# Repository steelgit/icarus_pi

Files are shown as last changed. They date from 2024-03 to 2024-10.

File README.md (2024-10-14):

# Icarus 🪽

Icarus is an open-source project that students or hobbyists can use as a base to gain experience with ROS2, SLAM, and Nav2. It is also a way for us to share our love of robotics! 

Icarus is a four-wheeled, mecanum-drive robot capable of manual and autonomous navigation. This is the project's main repository and contains all of the information and code to create the physical robot. Our sub-repo ([Icarus Jetson Nano Repository](https://github.com/steelgit/icarus_nano)) contains all of the information required to add autonomous navigation to the robot and can be used without recreating Icarus.

<br />

Icarus Video Video of Icarus Operating Autonomously

<br />
<br />

# Initial Run

>[Install the pigpio library](https://abyz.me.uk/rpi/pigpio/download.html)

>To install all of the required dependencies from the package.xml run:

    rosdep update --include-eol-distros    
<br />

    rosdep install --from-paths src -y --ignore-src --rosdistro foxy

<br />
<br />

# To Launch Icarus

>On startup, launch the PiGPIO Daemon using:

    sudo pigpiod

>Launch the robot!

    ros2 launch icarus_pi launch_robot.launch.py 

<br />
<br />

# To Launch Icarus in Simulation

>With Planar Controller:

    ros2 launch icarus_pi launch_sim_planar.launch.py 

>With Mecanum Controller:

    ros2 launch icarus_pi launch_sim_mecanum.launch.py 

<br />
<br />

# Materials List

Some of our core components include:

- Jetson Nano
- Raspberry Pi 4
- Motors with Quadrature Encoders
- Motor Controllers (L298N)
- 2-D LiDAR
- Raspberry Pi Camera V2
- Mecanum Wheels

<br />

A full list of our materials can be found on our [Materials List ](/docs/Materials%20List.pdf).

<br />
<br />

# Software

The Software for the Icarus Project is split between two devices, which requires having two different Ros2 workspaces.  The Raspberry Pi uses the Icarus_pi workspace in this repo, which contains the three main custom ROS2 packages: icarus_interface, icarus_pi, and mech_drive_controller.  Icarus_pi is the starting point for Icarus architecture and contains the robot description, launch files, and robot configuration files.  Except for PID tuning, all unique robot intrinsics are stored here and can be modified to fit different setups.  Icarus_interface is the Ros2 interface to the motor and encoders.  It leverages the PiGPIOd library to control GPIO signals on the Raspberry Pi, and will perform PID control when the interface is written to.  Finally, the mech_drive_controller is a custom ROS2 controller which allows two linear and one rotational movements.  These three packages work in tandem to manage all movement of the Icarus Robot and can run independent of icarus_nano. Icarus_nano contains three main ROS2 packages: autonomy, rplidar_ros, and camera_publisher. The autonomy package extends the slam_toolbox and Nav2 packages to enable support for holonmonic drive roborts. The rplidar_ros is cloned from the official Slamtec repository, (linked in the References section), and takes data from the physical LiDAR and translates it into a laser scan topic. The camera_publisher topic takes in information from our camera stream and publishes it so that we can see what the robot sees through RVIZ. 

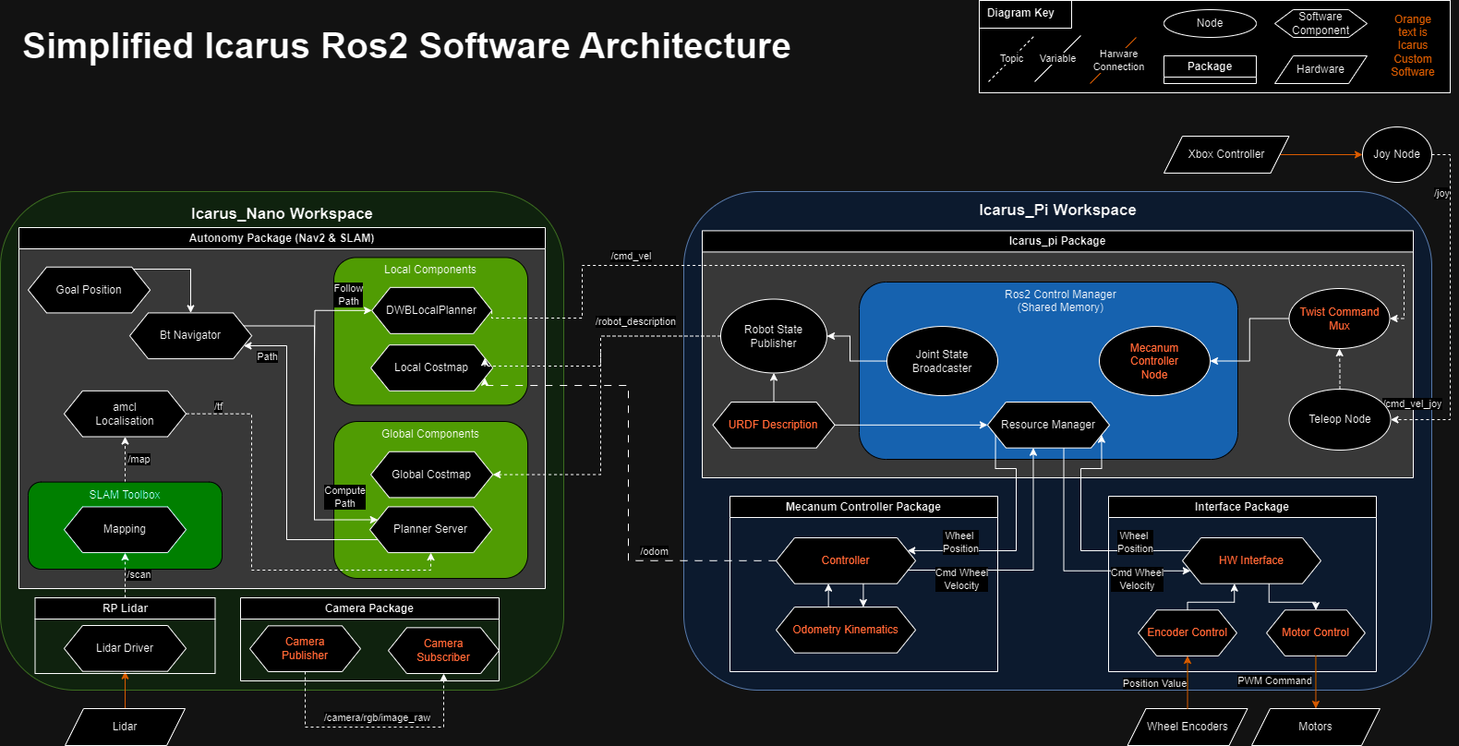
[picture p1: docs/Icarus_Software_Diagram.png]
Icarus Software Diagram Icarus Software Design


<br />
<br />

# Mechanical

The design of this robot was inspired by the turtlebot-burger educational platform. This design allows for a high degree of flexibility in the placement of components. Additionally, due to the modular design philosophy here, its possible to add, remove, or swap out new parts and sensors as you see fit. If desired, you can create your own custom fixtures and components to mount onto your robot as you see fit.
The mounting holes on the base plates have an initial diameter of 4.5mm in order for m3 flathead screws to sit flush within the plate, and then we have a 3.5mm diameter hole that's also designed for m3 screws; with a center-to-center distance of 20mm between each hole.
for a more vibration-resistant fit, add in threaded brass inserts to your mounting components by melting them in via soldering iron.

<br />

#### Mechanical Assembly

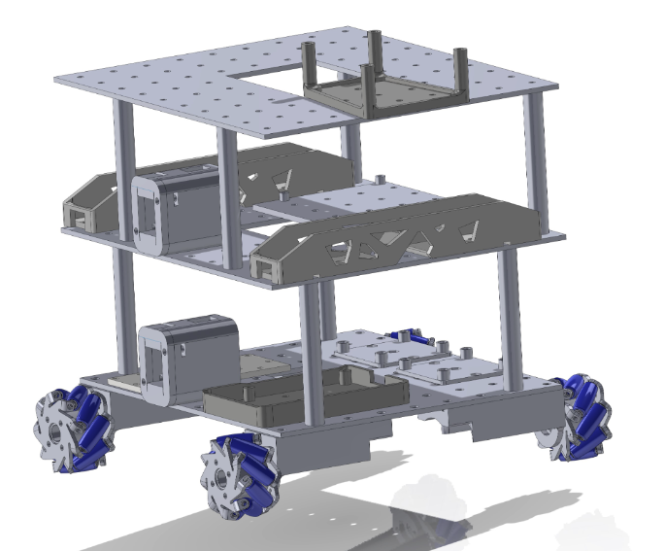
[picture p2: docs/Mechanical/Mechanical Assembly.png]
Icarus Mechanical Design


<br />

A more in-depth description of our mechanical design, as well as our STL files, can be found in our [Mechanical Documentation](/docs/Mechanical/Mechanical%20README.md).

<br />
<br />

# Electrical

Our electrical design was formulated around the core components that we wanted to use. These core components are listed above in the Material List section. We wanted to be able to operate the robot for a good amount of time before we needed to swap out or charge the batteries so that we could work on the project or test things for hours at a time. Because of this, and the fact that we used 12V motors, we opted for 
two 11.1 V, 5000 milli-amp hour batteries, one to power the motors, and one to power the rest of our electronics. We decided to solder as many of the components as we could for durability. The motors used jumper cable connections and since these could not be soldered easily, we decided to secure the connections with a layer of kapton tape. Our electrical diagram below shows how all of our components interact with each other.

<br />

#### Electrical Diagram

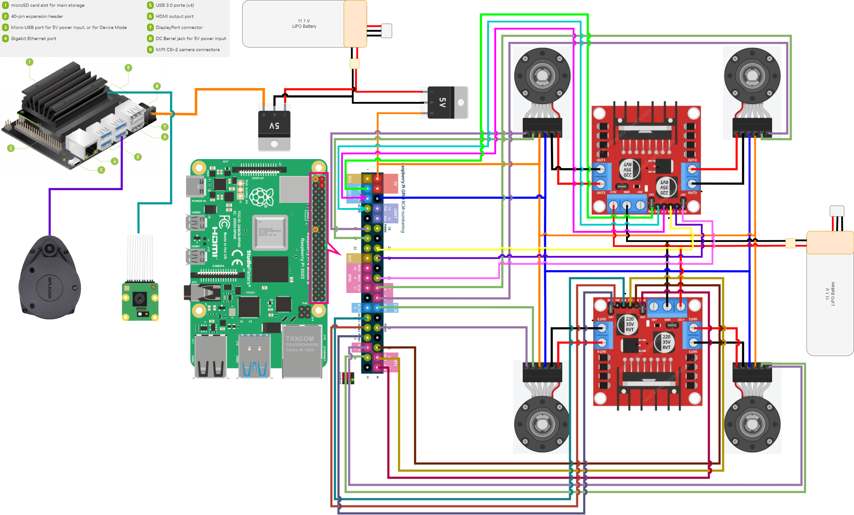
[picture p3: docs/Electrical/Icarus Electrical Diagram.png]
Icarus Electrical Diagram


<br />

A more in-depth description of our electrical design, as well as our [electrical schematic](docs/Electrical/Icarus%20Electrical%20Schematic.pdf) and [pinout descriptions](/docs/Electrical/Motor%20Connections%20Table.pdf), can be found in our [Electrical Documentation](/docs/Electrical/Electrical%20README.md).

<br />
<br />

# Mecanum Wheels

The Icarus Robot was created with the goal of controlling four Mecanum wheels.  Mecanum wheels that contain a circular array of smaller angled wheels.  This wheel arrangement allows movement in both the x and y linear directions, while still allowing a yaw rotation.  This also allows the robot to diagonally strafe or rotate while moving based on precise control of wheel speed and direction.  This required creating a custom controller package based on Ros2 control diff drive to allow the additional degree of movement.

<br />

#### Mecanum Wheel Kinematic Model

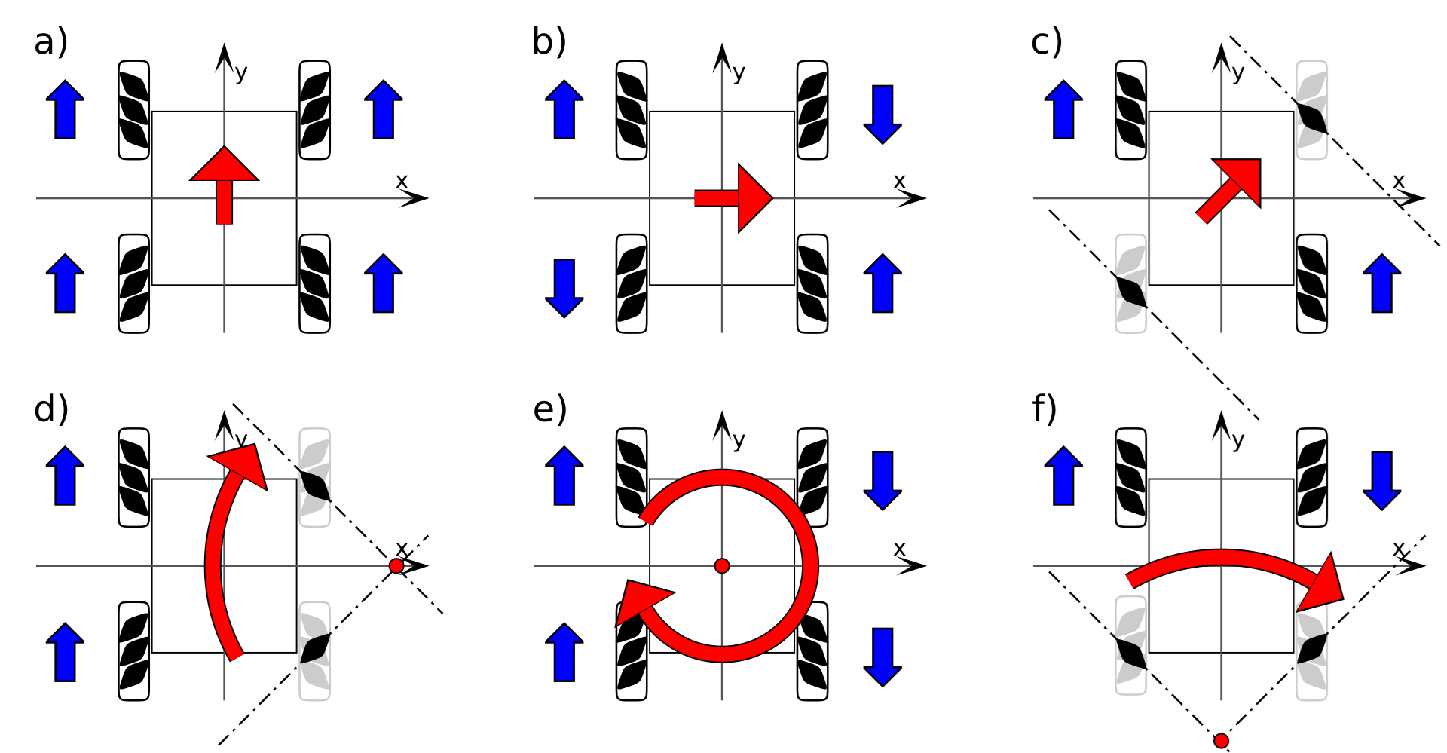
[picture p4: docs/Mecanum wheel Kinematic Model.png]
Mecanum Wheel Kinematic Model


#### Mecanum Wheel CAD Model

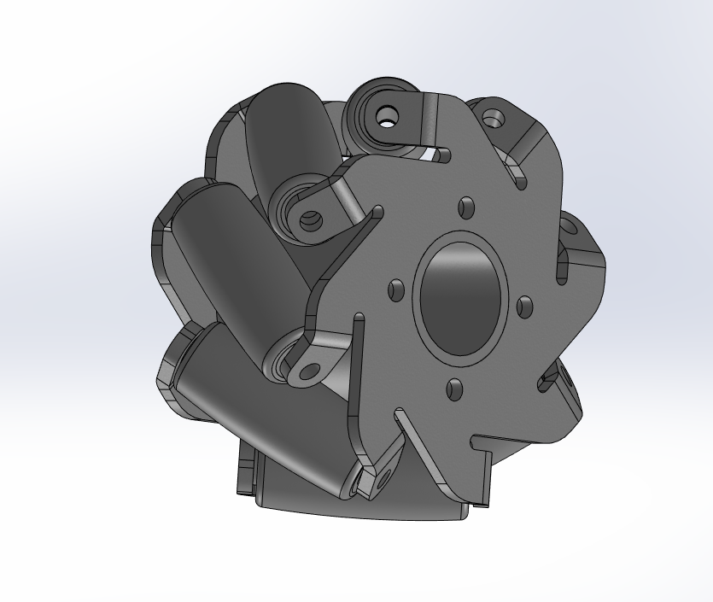
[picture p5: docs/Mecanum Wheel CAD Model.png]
Mecanum Wheel CAD Model


<br />

A more in-depth description of the various software challenges we faced with mecanum wheels can be found in our [Mecanum Wheel Documentation](/docs/Mecanum%20Wheel%20README.md).

<br />
<br />

# Lessons Learned & Future Improvements

Overall, we are quite happy with how Icarus turned out! However, looking back on our implementation, there are some things we would have done differently to achieve similar results while making our lives a little easier in the process. Some items that would have provided some relief to our major pain points include a more modular mechanical design, specifically for our component mounts, a simplified electrical design, and a change in the microcontrollers used. Addressing these issues would have allowed us to better utilize our time spent on Icarus. Below, we have detailed more improvements we would make in our 3 major categories: software, electrical, and mechanical. 

<br />

### Software

Our software design went through many iterations and required countless hours of discussion and design to get to our final product.  We learned three main lessons throughout the project's timeline when it came to our software process.  First, we should have filled out and shored up the project's foundational code before adding more software layers.  Debugging Nav2 and controller issues took significantly longer due to errors in our robot description and odometry calculation.  These could have been caught earlier and saved time later in the project if they had been a step at a time instead of simultaneously with the higher level software.  More early development in simulation would have been one way to catch these early issues.  The next lesson learned was that the group could have been more careful when researching embedded software version limits before progressing too far into setup.  The Jetson Nano cannot run Foxy or Humble natively, and Xubuntu on the Jetson Nano could only run up to Foxy.  This caused a version mismatch between some of our devices and the embedded system that led to errors later in the development cycle.  Finally, establish a common workflow for group members.  Our personal devices were setup independently, which caused members to not have the same tools or organization.  More communication on this area of the project would have made certain areas of our workflow run smoother.

-Be extra careful when reading hardware documentation.  Our LiDAR was mounted backwards, and caused the robot to move in unexpected directions.

<br />

### Electrical

The thing that we would like to improve upon in the future would be to simplify our electrical design. Our design greatly exceeds what was needed for the project, in terms of things like processing power and battery life. This is beneficial because we could easily integrate more features or sensors into the base design without worrying too much about power considerations or having to swap out the batteries too often. However, this also made the design take longer to assemble, which was detrimental to our objectives since we wanted to focus more on the software side of this project.

The switches were a nice addition, however, they could be removed to simplify the power and ground connections. Since the battery connectors are easily accessible, the system can be quickly de-energized without switches by simply disconnecting the connectors. There were also a couple of instances where wires had to be spliced 3 or more times. Creating these splices took us a little longer than initially expected, so using terminal blocks for connections instead of solder could make the assembly process quicker. Smaller milli-amp hour batteries could also be used to save on cost.

The biggest electrical change we would make would be to switch out our microcontrollers. Having the processing power of the Raspberry Pi and the Jetson Nano was nice, however, we could have accomplished everything we did with an Arduino and either a Raspberry Pi or Jetson Nano. The Arduino would control our motors and the rest of the processing would be offloaded onto the other microcontroller.

<br />

### Mechanical

It was never a wise decision to design something with the idea that we would never move the component from its position, or that it would need to be removed from its mounting area. Always design with ease of assembly and disassembly in mind

Make use of not only the horizontal space available on a given surface. If it's more convenient for assembly, create designs that take advantage of the vertical space given,
i.e.: mounting this vertically, upside down, stacked, etc.
<br />
<br />

# References

- [ROS2 Foxy Official Documentation](https://docs.ros.org/en/foxy/index.html)
- [The PiGPIO Library](https://abyz.me.uk/rpi/pigpio/index.html)
- [Articulated Robotics - Build a Mobile Robot with ROS](https://articulatedrobotics.xyz/tutorials/mobile-robot/project-overview)
- [ECAM Eurobot - Mecanum Wheels](https://ecam-eurobot.github.io/Tutorials/mechanical/mecanum.html)
- [Turtlebot3](https://www.turtlebot.com/turtlebot3/)

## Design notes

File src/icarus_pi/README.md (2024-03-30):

## Robot Package Template

This is a GitHub template. You can make your own copy by clicking the green "Use this template" button.

It is recommended that you keep the repo/package name the same, but if you do change it, ensure you do a "Find all" using your IDE (or the built-in GitHub IDE by hitting the `.` key) and rename all instances of `icarus_pi` to whatever your project's name is.

Note that each directory currently has at least one file in it to ensure that git tracks the files (and, consequently, that a fresh clone has direcctories present for CMake to find). These example files can be removed if required (and the directories can be removed if `CMakeLists.txt` is adjusted accordingly).

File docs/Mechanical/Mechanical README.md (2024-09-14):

# Information on Constructing the Robot
The following parts will need to have brass inserts melted into them. We accomplished this by using a soldering iron to heat up the plastic around the mounting holes and then using pliers to slide in the brass inserts.

- Raspberry Pi Holder (only where the pi mounts to the board)
- Motor Holders
- L298N Holder (where L298N mounts to board)
- Supports for each level
- Switch Carriages
- Nano mount
- RPLiDAR mount (where LiDAR mounts to the board, may need a smaller brass insert)

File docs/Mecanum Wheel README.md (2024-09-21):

### Mecanum Information
To provide this range of movement, Icarus is required to calculate individual wheel rotation velocities based on chassis velocity command.  The wheel velocities are calculated using the Mecanum Inverse kinematic formula as shown below.

$$\left(\begin{matrix}
\omega_{fl} &= \frac{1}{r} \left[v_x - v_y - (l_x + l_y)\omega_z \right ] \\ 
\omega_{fr} &= \frac{1}{r} \left[v_x + v_y + (l_x + l_y)\omega_z \right ] \\ 
\omega_{rl} &= \frac{1}{r} \left[v_x + v_y - (l_x + l_y)\omega_z \right ] \\ 
\omega_{rr} &= \frac{1}{r} \left[v_x - v_y + (l_x + l_y)\omega_z \right ] 
\end{matrix}\right)$$

The robot also publishes the Odometry of its movement, so it must calculate its actual speed and position.  Using the motor encoders to find wheel velocity, we use the Mecanum Kinematic Formula shown below to find its chassis velocity.

$$\left(\begin{matrix}
v_x & = (\omega_{fl} + \omega_{fr} + \omega_{rl} + \omega_{rr}) \cdot \frac{r}{4}\\ 
v_y & = (-\omega_{fl} + \omega_{fr} + \omega_{rl} - \omega_{rr}) \cdot \frac{r}{4}\\ 
\omega_z & = (-\omega_{fl} + \omega_{fr} - \omega_{rl} + \omega_{rr}) \cdot \frac{r}{4(l_x + l_y)}
\end{matrix}\right)$$

These equations and diagrams were sourced from the Ecam Eurobot, which can be found under references on the repo main page.

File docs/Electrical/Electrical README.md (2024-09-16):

# Electrical Information

Our electrical schematic below shows how our Raspberry Pi 4 connects to our quadrature motors and motor controller boards. It also highlights what connections are connected directly to our 12V batteries and what connections are connected to our regulated 5V rails. All of our 5V connections are spliced together with a common ground. Our 12V connections do the same.

We soldered together all of our connections, except for the wiring for our motors. These connections needed jumper cables so we used a pin-to-pin jumper connected to a pin-to-socket jumper to give us the length we needed. We wrapped the connection between the pin and socket with Kapton tape for added security and isolation. We also added a Raspberry Pi hat to the Raspberry Pi 4 that allowed us to solder those connections to ensure they would not vibrate loose. 

We added 5V regulators to our circuit to provide surge protection for our microcontrollers. This was needed since neither the Jetson Nano nor the Raspberry Pi 4 have proper over-voltage protection. Both of these microcontrollers need a microSD card. A 16 GB microSD will suffice for the features we have added, but to allow for new features, we would strongly recommend at least a 32 GB microSD card.

The LiDAR connects to the Jetson Nano via the USB ports. The Raspberry Pi 4 connects to the Jetson Nano via the CSI connector port. Due to the nominal current requirements of these two peripherals and the current needs of the Jetson Nano, it is necessary to power the Jetson Nano with the barrel jack rather than the micro-USB connection.

#### Electrical Schematic
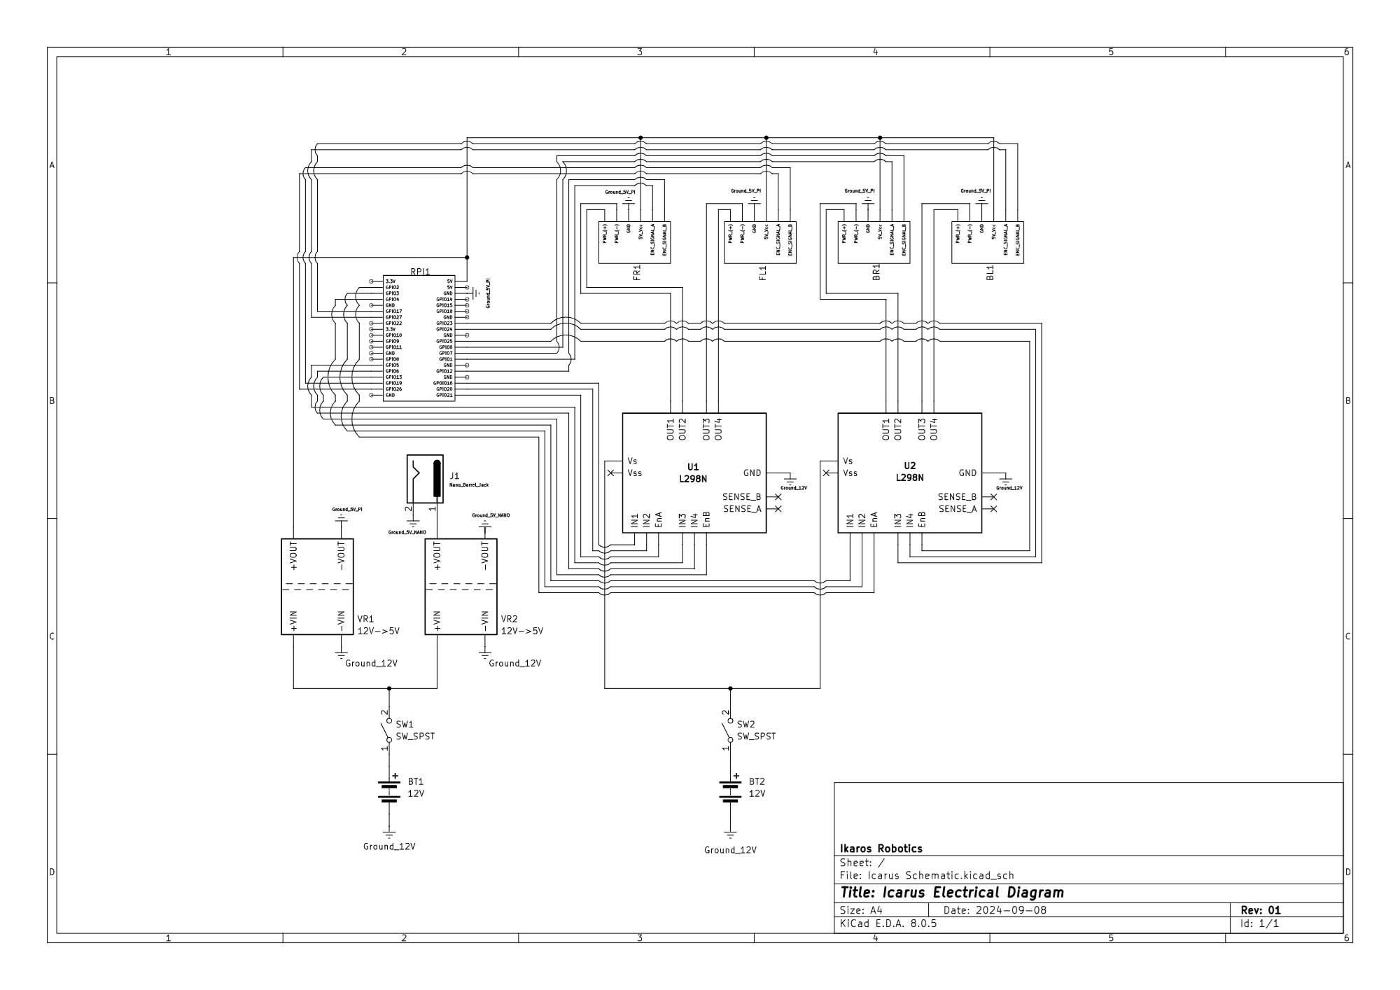
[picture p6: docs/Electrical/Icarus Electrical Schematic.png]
Icarus Electrical Schematic


#### Motor Pinout Table
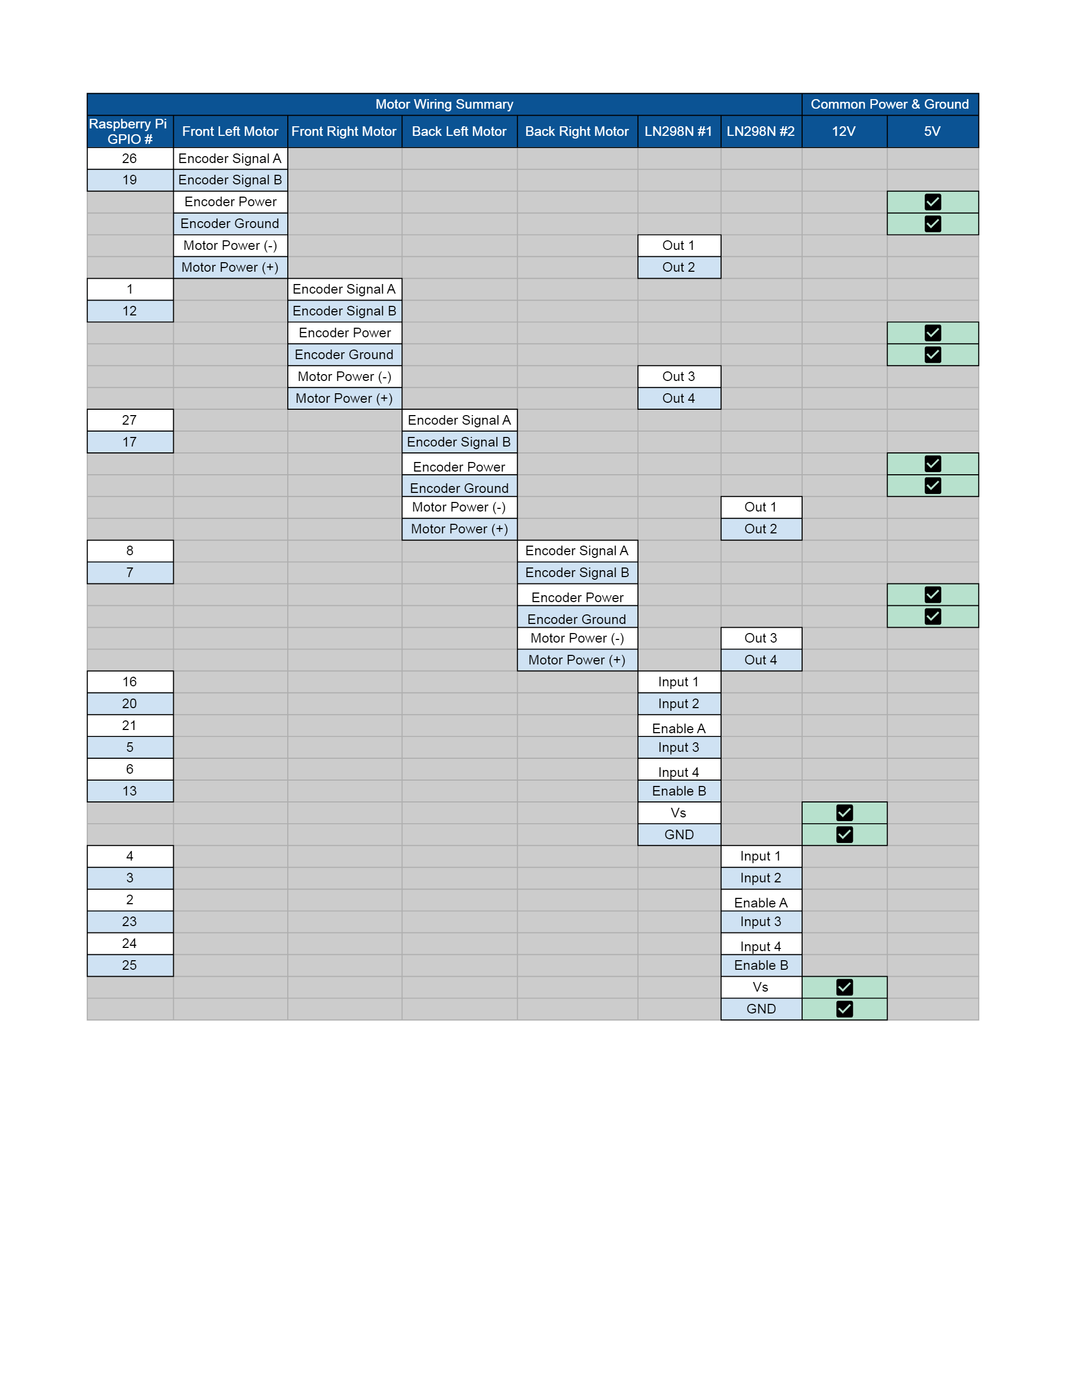
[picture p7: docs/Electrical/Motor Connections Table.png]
Icarus Motor Connections Table


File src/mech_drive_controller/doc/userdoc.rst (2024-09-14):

.. _mech_drive_controller_userdoc:

mech_drive_controller
=====================

Controller for mobile robots with Mecanum drive.
Input for control are robot body velocity commands which are translated to wheel commands for the Mecanum drive base.
Odometry is computed from hardware feedback and published.

Velocity commands
-----------------

The controller works with a velocity twist from which it extracts the x component of the linear velocity, the y component of the linear velocity. 
and the z component of the angular velocity. Velocities on other components are ignored.

Hardware interface type
-----------------------

The controller works with wheel joints through a velocity interface.

Other features
--------------

    Realtime-safe implementation.
    Odometry publishing
    Task-space velocity, acceleration and jerk limits
    Automatic stop after command time-out

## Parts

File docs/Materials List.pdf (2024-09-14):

Part, General | Part, Detailed | Distributor | Quantity | Single Unit Cost | Total Price | Website Link | $791.47
Jetson Nano | NVIDIA Jetson Nano 4gb Developer Kit (945-13450-0000-100) | Amazon | 1 | $149.00 | $149.00 | https://www.amazon.com/NVIDIA-Jetson-Nano-Developer-945-13450-0000-100/dp/B084DSDDLT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

cs&sprefix=nvidia+jetson+nan%2Celectronics%2C147&sr=1-3&ufe=app_do% 3Aamzn1.fos.f5122f16-c3e8-4386-bf32-63e904010ad0 (https://www.amazon.com/NVIDIA-Jetson-Nano-Developer-945-13450-0000-100/dp/B084DSDDLT?s=electronics)
Raspberry Pi 4 | Raspberry Pi 4 4GB Model B | Canakit | 1 | $55.00 | $55.00 | https://www.canakit.com/raspberry-pi-4-4gb.html
Motors with Encoder | 12V DC High Speed 130RPM Gear Motor with Encoder | Amazon | 4 | $14.88 | $59.52 | https://www.amazon.com/Encoder-Gearmotor-130RPM-Arduino- Printers/dp/B07GNGQ24C/ref=d_pd_di_sccai_cn_sccl_3_7/144-5710753-2053908? pd_rd_w=RNCcn&content-id=amzn1.sym.e13de93e-5518-4644-8e6b-4ee5f2e0b062&pf_rd_p=e13de93e-5518-4644-8e6b-4ee5f2e0b062&pf_rd_r=ESS2ZD0A2FKTD4WT5S7W&pd_rd_wg=mSxOC&pd_rd_r=5
| Mecanum Wheel Pair - 48mm Diameter (2 pair pack) | Amazon | 1 | $18.63 | $18.63 | d9fe69f-8b6e-4f44-afc0-f8e67c2f5f7f&pd_rd_i=B07GNGQ24C&psc=1 (https://www.amazon.com/Encoder-Gearmotor-130RPM-Arduino-Printers/dp/B07GNGQ24C) Wheels https://www.amazon.com/dp/B08TV1HGMG?psc=1&ref=ppx_yo2ov_dt_b_product_details (https://www.amazon.com/dp/B08TV1HGMG?psc=1&ref=ppx_yo2ov_dt_b_product_details)
Motor Driver Board | HiLetgo 4pcs L298N Motor Driver Board, DC Dual H-Bridge | Amazon | 1 | $11.49 | $11.49 | https://www.amazon.com/gp/product/B07BK1QL5T/ref=ppx_yo_dt_b_asin_title_o03_s00?ie=UTF8&psc=1 (https://www.amazon.com/gp/product/B07BK1QL5T/ref=ppx_yo_dt_b_asin_title_o03_s00?ie=UTF8&psc=1)
Wifi Card | Waveshare AC8265 Wireless NIC Module for Jetson Nano Supports 2.4GHz / 5GHz Dual Band WiFi and Bluetoth 4.2 | Amazon | 1 | $23.99 | $23.99 | https://www.amazon.com/gp/product/B07SGDRG34/ref=ppx_yo_dt_b_asin_title_o02_s00?ie=UTF8&psc=1 (https://www.amazon.com/gp/product/B07SGDRG34/ref=ppx_yo_dt_b_asin_title_o02_s00?ie=UTF8&psc=1)
16 AWG Wire | TUOFENG 16 awg Wire Solid Core, multicolor | Amazon | 1 | $19.99 | $19.99 | https://www.amazon.com/gp/product/B0C2TZYFDC/ref=ppx_yo_dt_b_asin_title_o08_s00?ie=UTF8&psc=1 (https://www.amazon.com/gp/product/B0C2TZYFDC/ref=ppx_yo_dt_b_asin_title_o08_s00?ie=UTF8&psc=1)
Solder | AUSTOR Pack of 6 Solder Wire 60-40 Rosin Core Solder 0.6mm, 1.8% flux | Amazon | 1 | $9.99 | $9.99 | https://www.amazon.com/gp/product/B0C2TZYFDC/ref=ppx_yo_dt_b_asin_title_o08_s00?ie=UTF8&psc=1 (https://www.amazon.com/gp/product/B0C2TZYFDC/ref=ppx_yo_dt_b_asin_title_o08_s00?ie=UTF8&psc=1)
11.1 V LiPo Batteries | HRB 2PCS 3S 5000mAh Lipo Battery 11.1V 50C 100C (2 pack) | Amazon | 1 | $79.99 | $79.99 | https://www.amazon.com/gp/product/B088QX4BMN/ref=ppx_yo_dt_b_asin_title_o07_s00?ie=UTF8&th=1 (https://www.amazon.com/gp/product/B088QX4BMN/ref=ppx_yo_dt_b_asin_title_o07_s00?ie=UTF8&th=1)
LiPo Battery Charger | Tenergy TB6AC+80W Balance Charger Discharger, 1S-6S | Amazon | 1 | $46.99 | $46.99 | https://www.amazon.com/gp/product/B010CCMWMO/ref=ppx_yo_dt_b_asin_title_o06_s00?ie=UTF8&psc=1 (https://www.amazon.com/gp/product/B010CCMWMO/ref=ppx_yo_dt_b_asin_title_o06_s00?ie=UTF8&psc=1)
LiDAR | Slamtec RPLIDAR A1M8 2D 360 Degree 12 Meters Scanning Radius LIDAR w/ USB adapter | Amazon | 1 | $99.00 | $99.00 | https://www.amazon.com/gp/product/B07TJW5SXF/ref=ppx_yo_dt_b_asin_title_o06_s01?ie=UTF8&psc=1 (https://www.amazon.com/gp/product/B07TJW5SXF/ref=ppx_yo_dt_b_asin_title_o06_s01?ie=UTF8&psc=1)
Velcro Straps | VELCRO Brand - ONE WRAP Thin Ties Reusable Light Duty, 8" x 1/2" Ties, 50 Count | Amazon | 1 | $5.27 | $5.27 | https://www.amazon.com/gp/product/B010BZYFKY/ref=ppx_yo_dt_b_asin_title_o06_s00?ie=UTF8&psc=1 (https://www.amazon.com/gp/product/B010BZYFKY/ref=ppx_yo_dt_b_asin_title_o06_s00?ie=UTF8&psc=1)
Raspberry Pi 4 Proto Shield | Raspberry Pi 3 Prototyping Board Proto Breadboard HAT by MakerSpot Soldered with Female Pin Connector PCB | Amazon | 1 | $14.99 | $14.99 | https://www.amazon.com/gp/product/B07B4TRVFD/ref=ppx_yo_dt_b_asin_title_o03_s00?ie=UTF8&th=1 (https://www.amazon.com/gp/product/B07B4TRVFD/ref=ppx_yo_dt_b_asin_title_o03_s00?ie=UTF8&th=1)
Barrel Jack to Bare Leads Adapter | DC Power Pigtails Cable,3FT DC 5.5MM x 2.1MM Male Plug, 16 AWG | Amazon | 1 | $9.99 | $9.99 | https://www.amazon.com/Pigtails-Female-Connector-Pigtail-Security/dp/B08PYWN3T7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. NkYSArlsMjrF0eRlcLB-v9baR4hXzNUbEnJEJs0aNPJ9tiJAKnKuJid6Ej2D_MrdKTbhnmwRISebxTBZuu-hNeGW1jXsOYcRXdiZ5DKdJkq7Q8IRxxmL0qpz8qeSIi5Ysuv0jTkpfoG6iMAJ859yY_i wUauZitlXEgiq6ItYgkQsENba_it7MeJe0sj-FrgQT_nYbYFCMWsofPf31SYDYj-REvkAelTALwvD2kqS_Bz0jjdrg3IJhmvq36FEk91gQjKNhMuKHiAEfqeeivLktpBeqOtCB

Qlg1JHCyCx1Fk0.iBmxCIdtxiT9RyIC-fW3zA2zfu66-vPVfOWEptHyLCg&dib_tag=se&keywords=barrel+jack+to+bare+leads+16+awg&qid= 1718670327&sprefix=barrel+jack+to+bare+leads+16+awg%2Caps%2C87&sr=8-3 (https://www.amazon.com/Pigtails-Female-Connector-Pigtail-Security/dp/B08PYWN3T7)
Zipties | Hyper Tough 4 inch 18lb Cable Ties 50 count (for wire management) | Walmart | 1 | $1.97 | $1.97 | https://walmart.com/ip/Hyper-Tough-4-inch-18lb-Cable-Ties-Natural-and-UV-Resistant-
MicroSD card | SanDisk 128GB | Walmart | 2 | $18.98 | $37.96 | https://www.walmart.com/ip/SanDisk-128GB-ImageMate-microSDXC-UHS-1-Up-to-140MB-s-SDSQUA4-128G-Aw6ka/525764488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 (https://www.walmart.com/ip/SanDisk-128GB-ImageMate-microSDXC-UHS-1-Up-to-140MB-s-SDSQUA4-128G-Aw6ka/525764488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)
Heat Shrink | 650pcs Heat Shrink Tubing Black innhom | Amazon | 1 | $9.95 | $9.95 | https://www.amazon.com/650pcs-Shrink-Tubing-innhom- Approved/dp/B07WWWPR2X/ref=sr_1_6? crid=1F98WKR655OUW&keywords=heat+shrinks&qid=1705348628&sprefix=heatsink

Black-50-Count/430028772?fulfillmentIntent=In-store&athbdg=L1102&from=/search (https://walmart.com/ip/Hyper-Tough-4-inch-18lb-Cable-Ties-Natural-and-UV-Resistant-Black-50-Count/430028772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)

s%2Caps%2C139&sr=8-6 (https://www.amazon.com/650pcs-Shrink-Tubing-innhom-Approved/dp/B07WWWPR2X)
Jumper Cables | EDGELEC 120pcs Breadboard Jumper Wires - Assorted (M-M, M-F, F-F) | Amazon | 1 | $6.98 | $6.98 | https://www.amazon.com/EDGELEC-Breadboard-Optional-Assorted- Multicolored/dp/B07GD2BWPY/ref=sr_1_3? crid=3CRLNZQPY4ZIU&keywords=jumper%2Bcables% 2Bpi&qid=1705348862&sprefix=jumper%2Bcables%2Bpi%2Caps%2C118&sr=8-3&th=1 (https://www.amazon.com/EDGELEC-Breadboard-Optional-Assorted-Multicolored/dp/B07GD2BWPY)
PLA Filament | PLA Basic | Bambu Lab | 1 | $27.99 | $27.99 | https://us.store.bambulab.com/products/pla-basic-filament
Voltage Regulators | [2 Pack] DC-DC 5A Buck Converter 4-38V to 1.25-36V Step-Down Voltage Regulator | Amazon | 1 | $13.99 | $13.99 | https://www.amazon.com/dp/B085T73CSD?ref_=cm_sw_r_apan_dp_75A0RFPFJSRSEEKG755Y&language=en-US (https://www.amazon.com/dp/B085T73CSD?ref_=cm_sw_r_apan_dp_75A0RFPFJSRSEEKG755Y&language=en-US)
Toggle Switches | DaierTek 12V Blue LED Illuminated Toggle Switch with Safety Cover Guard 3 Pin (2 pack) | Amazon | 1 | $7.99 | $7.99 | https://www.amazon.com/dp/B07SZJLNZY?ref_=cm_sw_r_apan_dp_MQV9J4HVMRDR0EHDFVW8&language=en-US&th=1 (https://www.amazon.com/dp/B07SZJLNZY?ref_=cm_sw_r_apan_dp_MQV9J4HVMRDR0EHDFVW8&language=en-US&th=1)
TRX to Bare Leads Connector | BDHI 3pcs Compatible with TRX Male Connectors 10cm 12awg Wire (3 pack) | Amazon | 1 | $8.98 | $8.98 | https://www.amazon.com/BDHI-Traxxas-Connectors-Turnigy-B140-3/dp/B082VWX62P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

12c4-8a8b-48a1-b9df-f2733305ed9d&pd_rd_i=B082VWX62P&psc=1 (https://www.amazon.com/BDHI-Traxxas-Connectors-Turnigy-B140-3/dp/B082VWX62P)

TRX to Banana Jack Charging Harness

BINYEAE FLASH HOBBY 2pcs T Male to 4.0mm Banana Plug Connector Adaptor Cable14AWG
Amazon | 1 | $6.99 | $6.99

https://www.amazon.com/BINYEAE-FLASH-HOBBY-Male-4-0mm/dp/B07KS2V772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 (https://www.amazon.com/BINYEAE-FLASH-HOBBY-Male-4-0mm/dp/B07KS2V772)
Brass Inserts Kit | Hilitchi 460 Pcs M2 M3 M4 M5 Female Thread Brass Knurled Threaded Insert Embedment Nuts Assortment Kit | Amazon | 1 | $19.89 | $19.89 | https://www.amazon.com/DYWISHKEY-Pieces-Female-Standoff- Assortment/dp/B07MW5P8JH/ref=sr_1_3?keywords=hex% 2Bspacers&qid=1677982233&s=industrial&sr=1-3&th=1 (https://www.amazon.com/DYWISHKEY-Pieces-Female-Standoff-Assortment/dp/B07MW5P8JH?s=industrial)
Metric Screw/Nut Kit | Guard4U 480Pcs 12-Size Metric M2 M2.5 M3 Stainless Steel Phillips Pan Head | Amazon | 1 | $14.99 | $14.99 | https://www.amazon.com/Guard4U-12-Size-Stainless-Phillips- Assortment/dp/B08LW63JKL/ref=sr_1_3? crid=3GUS78OM5KTR0&keywords=metric+screws+assortment+kit+m2+m2. 5+m3+phillips&qid=1705350161&s=industrial&sprefix=metric+screws+assortment+kit+ (https://www.amazon.com/Guard4U-12-Size-Stainless-Phillips-Assortment/dp/B08LW63JKL?s=industrial) m2+m2.5+m3+phillips%2Cindustrial%2C116&sr=1-3
Camera | Raspberry Pi Camera Board v2 - 8 Megapixels | Adafruit | 1 | $29.95 | $29.95 | https://www.adafruit.com/product/3099
| | Amazon | 1 | | $0.00
The below parts are recommended for prototyping | | | | | | | $21.68
Raspberry Pi 4 Power Supply | Raspberry Pi 4 Power Supply (USB-C) - Black | Canakit | 1 | $8.00 | $8.00 | https://www.canakit.com/official-raspberry-pi-4-power-supply-black.html
Micro HDMI cable | UGREEN Micro HDMI to HDMI Cable Adapter 4K 60Hz Ethernet | Amazon | 1 | $8.99 | $8.99 | https://www.amazon.com/UGREEN-Adapter-Ethernet-Compatible- Raspberry/dp/B06WWQ7KLV/ref=sr_1_9?crid=2OC8DHBFOG5I2&keywords=micro% 2Bhdmi%2Bcable&qid=1705348026&sprefix=micro%2Bhdmi%2Bcable%2Caps% 2C114&sr=8-9&th=1 (https://www.amazon.com/UGREEN-Adapter-Ethernet-Compatible-Raspberry/dp/B06WWQ7KLV)
Jetson Nano Wall Power Supply | COOLM AC 100-240V to DC 5V/4A 20W Charger Plug DC 5.5mm x 2.5 mm (for prototyping) | Amazon | 1 | $13.68 | $13.68 | https://www.amazon.com/gp/product/B07RTWD725/ref=ppx_yo_dt_b_asin_title_o02_s00?ie=UTF8&psc=1 (https://www.amazon.com/gp/product/B07RTWD725/ref=ppx_yo_dt_b_asin_title_o02_s00?ie=UTF8&psc=1)

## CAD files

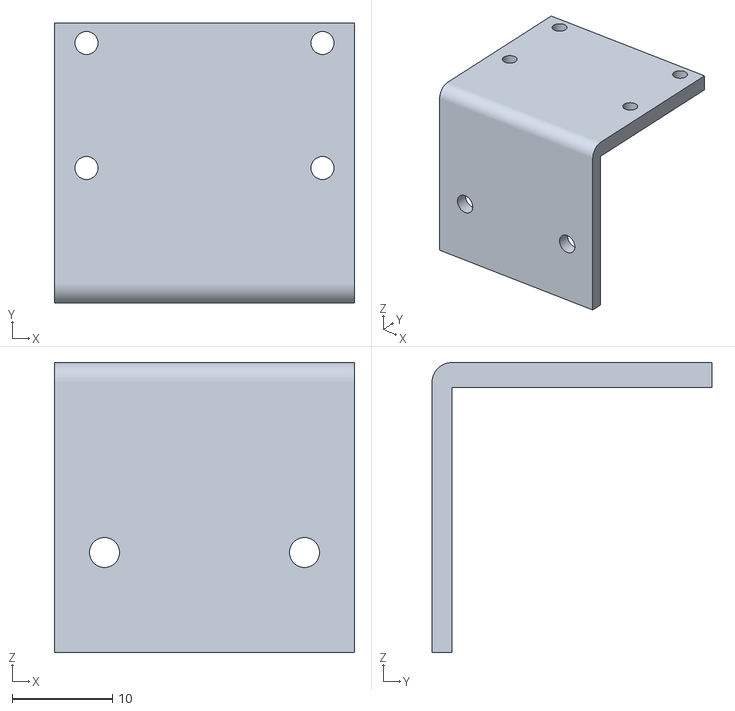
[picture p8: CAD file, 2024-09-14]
docs/Mechanical/Camera Mount.STL
30.0 x 28.0 x 29.0

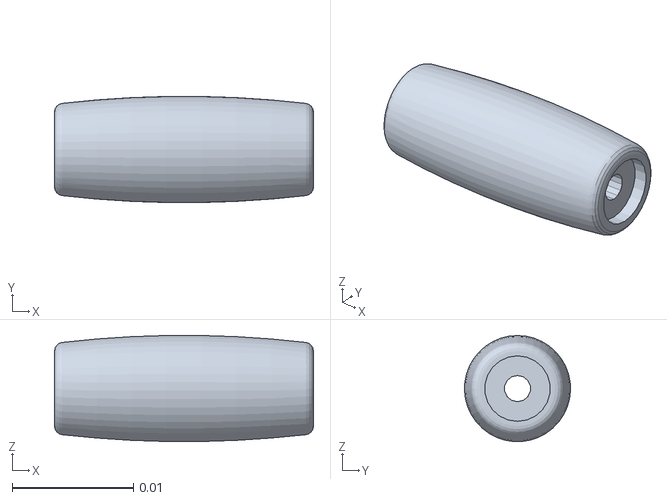
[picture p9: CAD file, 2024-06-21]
src/icarus_pi/Mesh/Mecanum-Left/meshes/Mecanum_roller_link_8.STL
0.0213 x 0.00874 x 0.00874

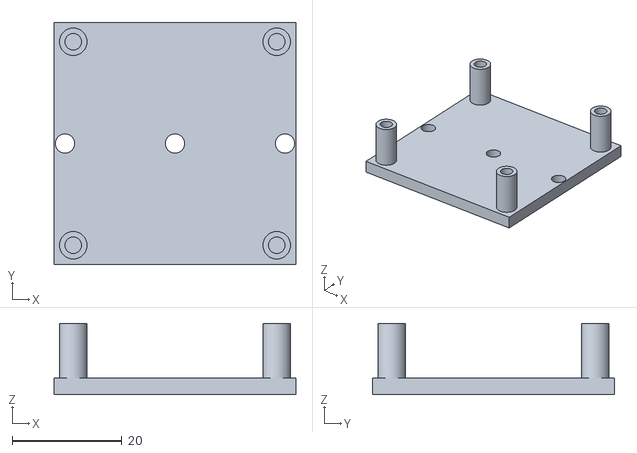
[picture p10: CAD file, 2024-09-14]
docs/Mechanical/L298N Holder.stl
44.0 x 44.0 x 13.0

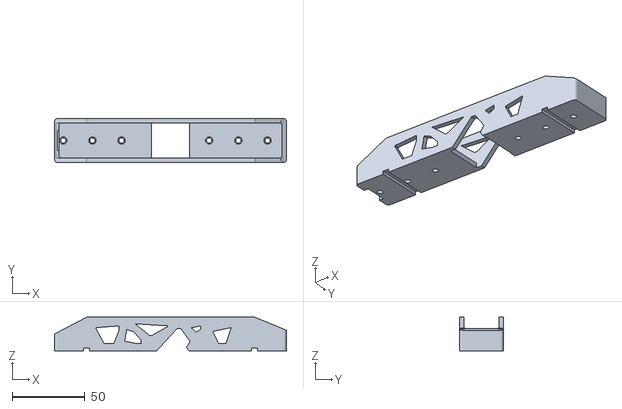
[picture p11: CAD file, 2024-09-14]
docs/Mechanical/Battery Holder V2.STL
159.0 x 30.0 x 23.0

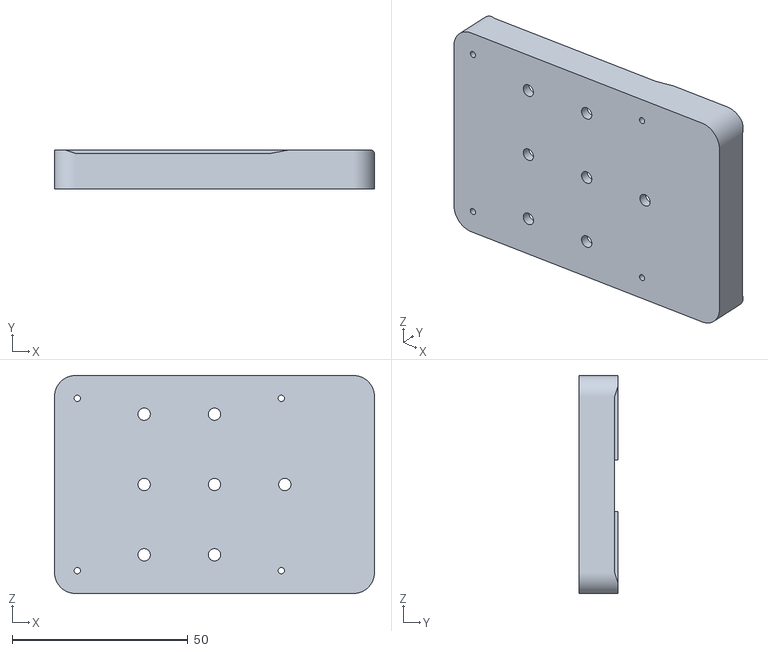
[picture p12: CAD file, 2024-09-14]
docs/Mechanical/nikodembartnik-1-raspberry_pi_holder_3.STL
91.0 x 11.1 x 62.0

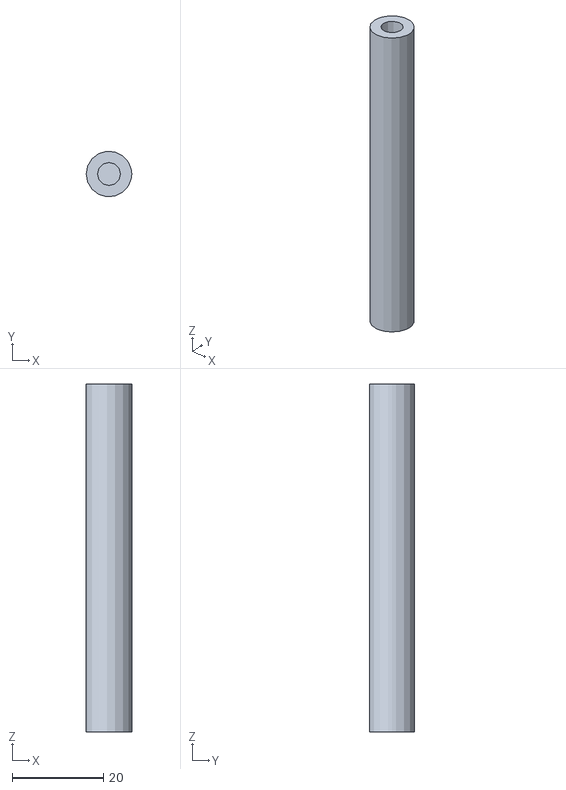
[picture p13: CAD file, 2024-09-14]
docs/Mechanical/Level Support.STL
10.0 x 9.96 x 76.2

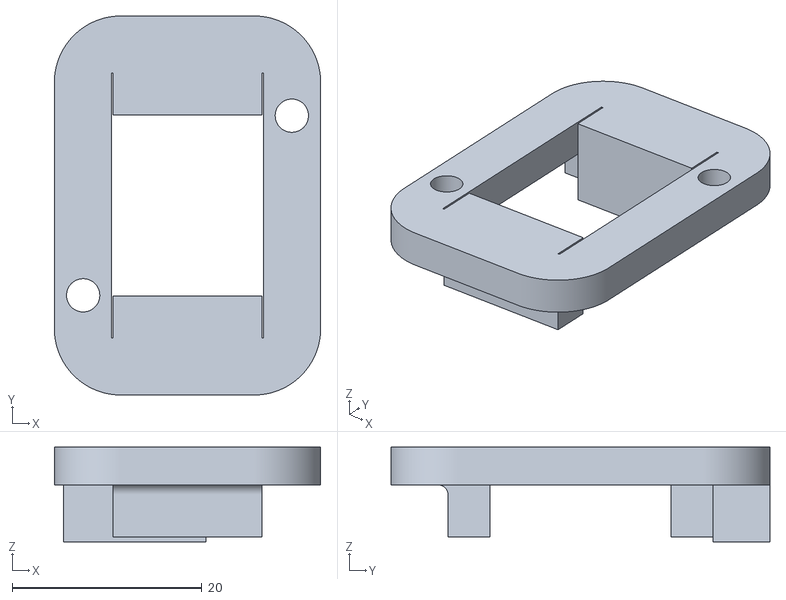
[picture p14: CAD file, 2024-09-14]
docs/Mechanical/Switch-Jig top.STL
28.0 x 39.9 x 10.0

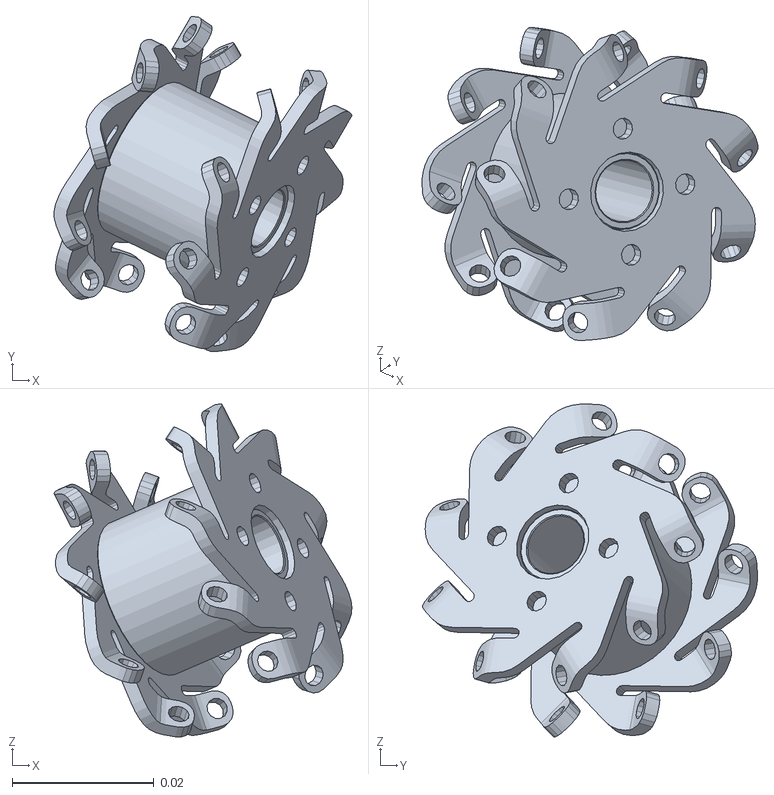
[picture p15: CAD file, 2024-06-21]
src/icarus_pi/Mesh/Mecanum-Right/meshes/Right_Base_Link.STL
0.0421 x 0.0474 x 0.0471

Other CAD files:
src/icarus_pi/Mesh/Mecanum-Right/meshes/Mecanum_Roller_Link4.STL
src/icarus_pi/Mesh/Mecanum-Left/meshes/Mecanum_roller_link_6.STL
src/icarus_pi/Mesh/Mecanum-Right/meshes/Mecanum_Roller_Link3.STL
src/icarus_pi/Mesh/Mecanum-Left/meshes/Mecanum_roller_link_2.STL
src/icarus_pi/Mesh/Mecanum-Right/meshes/Mecanum_Roller_Link8.STL
src/icarus_pi/Mesh/Mecanum-Left/meshes/Mecanum_roller_link_5.STL
src/icarus_pi/Mesh/Mecanum-Right/meshes/Mecanum_Roller_Link9.STL
src/icarus_pi/Mesh/Mecanum-Left/meshes/Mecanum_roller_link_4.STL
src/icarus_pi/Mesh/Mecanum-Right/meshes/Mecanum_Roller_Link1.STL
src/icarus_pi/Mesh/Mecanum-Left/meshes/Mecanum_roller_link_9.STL
docs/Mechanical/Buck Converter Holder.STL
docs/Mechanical/Level 1.STL
docs/Mechanical/Nano Holder.STL
docs/Mechanical/Switch Jig-Box.STL
docs/Mechanical/nikodembartnik-48-rplidar_holder.STL
docs/Mechanical/upper levels.STL
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

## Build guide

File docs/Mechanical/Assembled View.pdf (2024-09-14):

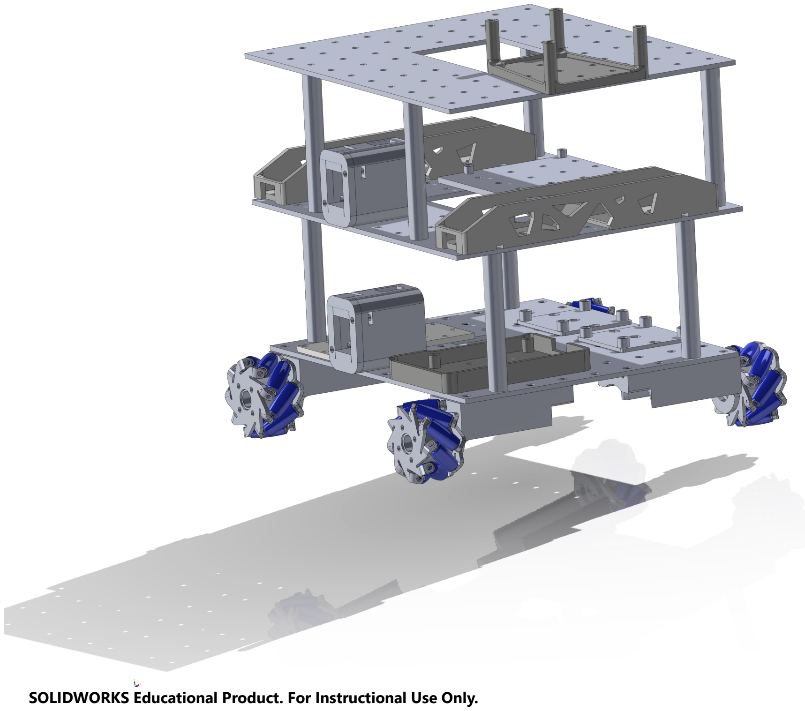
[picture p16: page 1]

SOLIDWORKS Educational Product. For Instructional Use Only.

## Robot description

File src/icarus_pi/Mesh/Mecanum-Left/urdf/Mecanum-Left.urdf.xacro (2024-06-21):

<?xml version="1.0"?>

<robot name="Mecanum-Left" xmlns:xacro="http://www.ros.org/wiki/xacro" >
  <link name="base_link">
    <inertial>
      <origin xyz="-5.71071320654166E-07 1.24074703998625E-17 -8.40087960733809E-19" rpy="0 0 0" />
      <mass value="0.0110925597603563" />
      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
    </inertial>
    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
  </link>
  <link name="Mecanum_roller_link_1">
    <inertial>
      <origin xyz="4.19537259525784E-05 -9.19403442267708E-17 -4.5102810375397E-17" rpy="0 0 0" />
      <mass value="0.00104310145784987" />
      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
    </inertial>
    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
  </link>
  <joint name="Mecanum_roller_joint_1" type="continuous">
    <origin xyz="0.00012912 0.014344 0.0095825" rpy="-2.7656 0.6249 2.6298" />
    <parent link="base_link" />
    <child link="Mecanum_roller_link_1" />
    <axis xyz="1 0 0" />
  </joint>
  <link name="Mecanum_roller_link_2">
    <inertial>
      <origin xyz="-4.19537259514885E-05 -2.77555756156289E-17 -9.71445146547012E-17" rpy="0 0 0" />
      <mass value="0.00104310145784987" />
      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
    </inertial>
    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
  </link>
  <joint name="Mecanum_roller_joint_2" type="continuous">
    <origin xyz="-0.00012933 0.0045802 0.016631" rpy="1.6775 -0.19406 -0.76608" />
    <parent link="base_link" />
    <child link="Mecanum_roller_link_2" />
    <axis xyz="1 0 0" />
  </joint>
  <link name="Mecanum_roller_link_3">
    <inertial>
      <origin xyz="-4.19537259517232E-05 6.24500451351651E-17 -1.45716771982052E-16" rpy="0 0 0" />
      <mass value="0.00104310145784987" />
      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
    </inertial>
    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
  </link>
  <joint name="Mecanum_roller_joint_3" type="continuous">
    <origin xyz="0.00012912 -0.006946 0.01579" rpy="1.4846 0.29377 -0.73958" />
    <parent link="base_link" />
    <child link="Mecanum_roller_link_3" />
    <axis xyz="1 0 0" />
  </joint>
  <link name="Mecanum_roller_link_4">
    <inertial>
      <origin xyz="-4.19537259518845E-05 9.54097911787244E-17 -5.03069808033274E-17" rpy="0 0 0" />
      <mass value="0.00104310145784987" />
      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
    </inertial>
    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
  </link>
  <joint name="Mecanum_roller_joint_4" type="continuous">
    <origin xyz="0.00012912 -0.015471 0.0076312" rpy="1.4497 0.68992 -0.41086" />
    <parent link="base_link" />
    <child link="Mecanum_roller_link_4" />
    <axis xyz="1 0 0" />
  </joint>
  <link name="Mecanum_roller_link_5">
    <inertial>
      <origin xyz="4.1659597956364E-05 1.04950770296597E-16 1.38777878078145E-17" rpy="0 0 0" />
      <mass value="0.00104310145784987" />
      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
    </inertial>
    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
  </link>
  <joint name="Mecanum_roller_joint_5" type="continuous">
    <origin xyz="0.00012912 -0.016757 -0.0040986" rpy="1.6948 0.7554 0.24013" />
    <parent link="base_link" />
    <child link="Mecanum_roller_link_5" />
    <axis xyz="1 0 0" />
  </joint>
  <link name="Mecanum_roller_link_6">
    <inertial>
      <origin xyz="-4.19537259515289E-05 6.93889390390723E-18 1.73472347597681E-18" rpy="0 0 0" />
      <mass value="0.00104310145784984" />
      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
    </inertial>
    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
  </link>
  <joint name="Mecanum_roller_joint_6" type="continuous">
    <origin xyz="0.00012912 -0.010202 -0.013911" rpy="1.7524 0.42673 0.68129" />
    <parent link="base_link" />
    <child link="Mecanum_roller_link_6" />
    <axis xyz="1 0 0" />
  </joint>
  <link name="Mecanum_roller_link_7">
    <inertial>
      <origin xyz="-4.19537259513104E-05 6.24500451351651E-17 4.16333634234434E-17" rpy="0 0 0" />
      <mass value="0.00104310145784987" />
      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
    </inertial>
    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
  </link>
  <joint name="Mecanum_roller_joint_7" type="continuous">
    <origin xyz="0.00012912 0.0011266 -0.017214" rpy="2.5112 -0.051481 0.78407" />
    <parent link="base_link" />
    <child link="Mecanum_roller_link_7" />
    <axis xyz="1 0 0" />
  </joint>
  <link name="Mecanum_roller_link_8">
    <inertial>
      <origin xyz="4.16595979570254E-05 -8.67361737988404E-18 -6.93889390390723E-18" rpy="0 0 0" />
      <mass value="0.00104310145784987" />
      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
    </inertial>
    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
  </link>
  <joint name="Mecanum_roller_joint_8" type="continuous">
    <origin xyz="-0.00012933 0.012113 -0.012282" rpy="-1.7252 -0.51523 0.6222" />
    <parent link="base_link" />
    <child link="Mecanum_roller_link_8" />
    <axis xyz="1 0 0" />
  </joint>
  <link name="Mecanum_roller_link_9">
    <inertial>
      <origin xyz="-4.19537259509657E-05 8.02309607639273E-17 -1.04083408558608E-17" rpy="0 0 0" />
      <mass value="0.00104310145784987" />
      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
    </inertial>
    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
  </link>
  <joint name="Mecanum_roller_joint_9" type="continuous">
    <origin xyz="0.00012912 0.017148 -0.0018797" rpy="1.5575 -0.78024 0.10117" />
    <parent link="base_link" />
    <child link="Mecanum_roller_link_9" />
    <axis xyz="1 0 0" />
  </joint>

    <ros2_control name="gazeboSimSystem" type="system">	
		<hardware>
			<plugin>gazebo_ros2_control/GazeboSystem</plugin>
		</hardware>

		<joint name="Mecanum_roller_joint_1">
			<command_interface name="velocity">
				<param name="min">-100</param>
				<param name="max">100</param>
			</command_interface>
			<state_interface name="position"/>
			<state_interface name="velocity"/>
		</joint>

		<joint name="Mecanum_roller_joint_2">
			<command_interface name="velocity">
				<param name="min">-100</param>
				<param name="max">100</param>
			</command_interface>
			<state_interface name="position"/>
			<state_interface name="velocity"/>
		</joint>

    		<joint name="Mecanum_roller_joint_3">
			<command_interface name="velocity">
				<param name="min">-100</param>
				<param name="max">100</param>
			</command_interface>
			<state_interface name="position"/>
			<state_interface name="velocity"/>
		</joint>

    		<joint name="Mecanum_roller_joint_4">
			<command_interface name="velocity">
				<param name="min">-100</param>
				<param name="max">100</param>
			</command_interface>
			<state_interface name="position"/>
			<state_interface name="velocity"/>
		</joint>

    		<joint name="Mecanum_roller_joint_5">
			<command_interface name="velocity">
				<param name="min">-100</param>
				<param name="max">100</param>
			</command_interface>
			<state_interface name="position"/>
			<state_interface name="velocity"/>
		</joint>

    		<joint name="Mecanum_roller_joint_6">
			<command_interface name="velocity">
				<param name="min">-100</param>
				<param name="max">100</param>
			</command_interface>
			<state_interface name="position"/>
			<state_interface name="velocity"/>
		</joint>

    		<joint name="Mecanum_roller_joint_7">
			<command_interface name="velocity">
				<param name="min">-100</param>
				<param name="max">100</param>
			</command_interface>
			<state_interface name="position"/>
			<state_interface name="velocity"/>
		</joint>

    		<joint name="Mecanum_roller_joint_8">
			<command_interface name="velocity">
				<param name="min">-100</param>
				<param name="max">100</param>
			</command_interface>
			<state_interface name="position"/>
			<state_interface name="velocity"/>
		</joint>

    		<joint name="Mecanum_roller_joint_9">
			<command_interface name="velocity">
				<param name="min">-100</param>
				<param name="max">100</param>
			</command_interface>
			<state_interface name="position"/>
			<state_interface name="velocity"/>
		</joint>
	</ros2_control>

  	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


</robot>

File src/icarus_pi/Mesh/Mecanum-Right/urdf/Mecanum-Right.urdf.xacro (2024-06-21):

<?xml version="1.0" encoding="utf-8"?>
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
<robot name="Mecanum-Right">
  <link name="Right_Base_Link">
    <inertial>
      <origin xyz="-4.7771233839358E-07 2.34552518933002E-07 -2.07119508697187E-07" rpy="0 0 0" />
      <mass value="0.0110925597603562" />
      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
    </inertial>
    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
  </link>
  <link name="Mecanum_Roller_Link1">
    <inertial>
      <origin xyz="-4.16595979552251E-05 0 1.56125112837913E-17" rpy="0 0 0" />
      <mass value="0.00104310145784987" />
      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
    </inertial>
    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
  </link>
  <joint name="Mecanum_Roller_Joint_1" type="continuous">
    <origin xyz="-0.00786276516006295 -0.00229210366796707 0.0151828566548909" rpy="-1.36068806852681 0.491674447872911 -2.73783219400761" />
    <parent link="Right_Base_Link" />
    <child link="Mecanum_Roller_Link1" />
    <axis xyz="1 0 0" />
  </joint>
  <link name="Mecanum_Roller_Link2">
    <inertial>
      <origin xyz="-4.19537259518619E-05 5.55111512312578E-17 4.5102810375397E-17" rpy="0 0 0" />
      <mass value="0.00104310145784987" />
      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
    </inertial>
    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
  </link>
  <joint name="Mecanum_Roller_Joint_2" type="continuous">
    <origin xyz="-0.00257449912034201 0.00825350947765706 0.0149280771357719" rpy="1.93542758330994 -0.0214038442701011 0.265392618762669" />
    <parent link="Right_Base_Link" />
    <child link="Mecanum_Roller_Link2" />
    <axis xyz="1 0 0" />
  </joint>
  <link name="Mecanum_Roller_Link3">
    <inertial>
      <origin xyz="-4.16595979550827E-05 -1.73472347597681E-18 -1.73472347597681E-18" rpy="0 0 0" />
      <mass value="0.00104310145784987" />
      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
    </inertial>
    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
  </link>
  <joint name="Mecanum_Roller_Joint_3" type="continuous">
    <origin xyz="0.0038677825728569 0.0149620683207087 0.00766633686486059" rpy="-1.45997240902279 -0.325004631734415 3.05656776956051" />
    <parent link="Right_Base_Link" />
    <child link="Mecanum_Roller_Link3" />
    <axis xyz="1 0 0" />
  </joint>
  <link name="Mecanum_Roller_Link4">
    <inertial>
      <origin xyz="4.16595979567443E-05 0 -1.73472347597681E-18" rpy="0 0 0" />
      <mass value="0.00104310145784984" />
      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
    </inertial>
    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
  </link>
  <joint name="Mecanum_Roller_Joint_4" type="continuous">
    <origin xyz="0.00844966471730028 0.0146945636211975 -0.00320451517983013" rpy="-1.23509707840396 0.401303910502291 -0.602154738197085" />
    <parent link="Right_Base_Link" />
    <child link="Mecanum_Roller_Link4" />
    <axis xyz="1 0 0" />
  </joint>
  <link name="Mecanum_Roller_Link5">
    <inertial>
      <origin xyz="4.16595979569898E-05 3.64291929955129E-17 -1.38777878078145E-17" rpy="0 0 0" />
      <mass value="0.0010431014578499" />
      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
    </inertial>
    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
  </link>
  <joint name="Mecanum_Roller_Joint_5" type="continuous">
    <origin xyz="0.00902723373565527 0.0075761638010083 -0.0125978865105267" rpy="1.01038415879456 0.159830081855345 -1.04575970415485" />
    <parent link="Right_Base_Link" />
    <child link="Mecanum_Roller_Link5" />
    <axis xyz="1 0 0" />
  </joint>
  <link name="Mecanum_Roller_Link6">
    <inertial>
      <origin xyz="4.16595979573133E-05 -6.93889390390723E-18 1.73472347597681E-18" rpy="0 0 0" />
      <mass value="0.00104310145784987" />
      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
    </inertial>
    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
  </link>
  <joint name="Mecanum_Roller_Joint_6" type="continuous">
    <origin xyz="0.00533023866526893 -0.00306235275179063 -0.0161185142859026" rpy="-1.00833638122774 -0.270056335980709 -1.28003202448786" />
    <parent link="Right_Base_Link" />
    <child link="Mecanum_Roller_Link6" />
    <axis xyz="1 0 0" />
  </joint>
  <link name="Mecanum_Roller_Link7">
    <inertial>
      <origin xyz="4.19537259526218E-05 2.94902990916057E-17 1.38777878078145E-17" rpy="0 0 0" />
      <mass value="0.00104310145784982" />
      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
    </inertial>
    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
  </link>
  <joint name="Mecanum_Roller_Joint_7" type="continuous">
    <origin xyz="-0.000911455412901512 -0.0122431059082033 -0.0121190576424399" rpy="0.755293558147071 0.758576984655219 1.85745610617137" />
    <parent link="Right_Base_Link" />
    <child link="Mecanum_Roller_Link7" />
    <axis xyz="1 0 0" />
  </joint>
  <link name="Mecanum_Roller_Link8">
    <inertial>
      <origin xyz="-4.19537259514699E-05 1.38777878078145E-17 -1.21430643318376E-17" rpy="0 0 0" />
      <mass value="0.00104310145784987" />
      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
    </inertial>
    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
  </link>
  <joint name="Mecanum_Roller_Joint_8" type="continuous">
    <origin xyz="-0.00677729047097743 -0.0156703192336383 -0.00247090679262434" rpy="2.95463100680286 -1.13639269714102 -0.725426795925048" />
    <parent link="Right_Base_Link" />
    <child link="Mecanum_Roller_Link8" />
    <axis xyz="1 0 0" />
  </joint>
  <link name="Mecanum_Roller_Link9">
    <inertial>
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

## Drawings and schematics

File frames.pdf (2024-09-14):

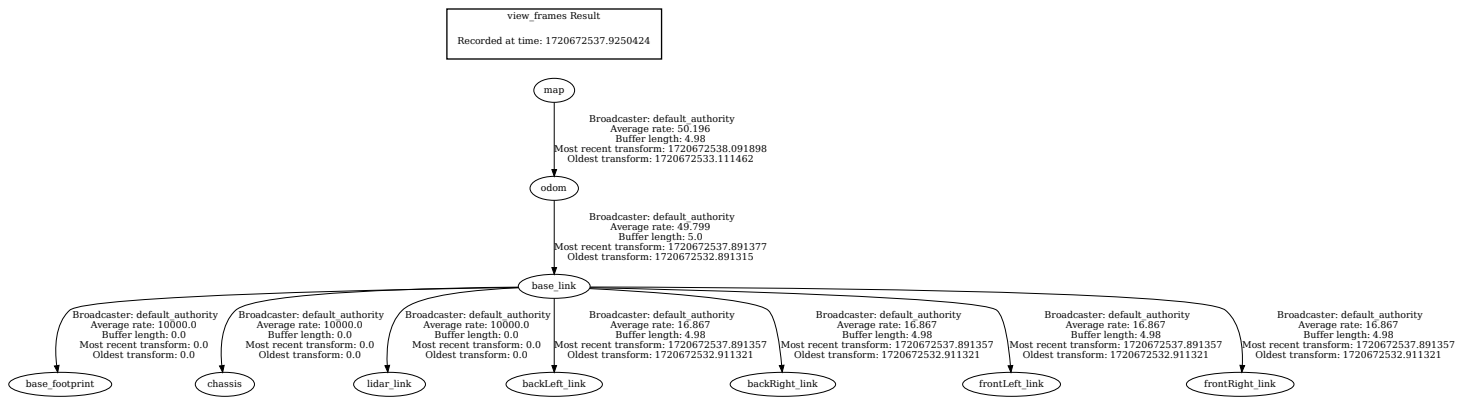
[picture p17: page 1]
view_frames Result; odom; base_link; Broadcaster: default_authority Average rate: 49.799 Buffer length: 5.0; base_footprint; chassis; lidar_link; backLeft_link; Broadcaster: default_authority Average rate: 16.867 Buffer length: 4.98; backRight_link; frontLeft_link; frontRight_link; map; Broadcaster: default_authority Average rate: 50.196 Buffer length: 4.98

Recorded at time: 1720672537.9250424

Most recent transform: 1720672538.091898
Oldest transform: 1720672533.111462

Most recent transform: 1720672537.891377
Oldest transform: 1720672532.891315

Broadcaster: default_authority
Average rate: 10000.0
Buffer length: 0.0
Most recent transform: 0.0
Oldest transform: 0.0

Most recent transform: 1720672537.891357
Oldest transform: 1720672532.911321

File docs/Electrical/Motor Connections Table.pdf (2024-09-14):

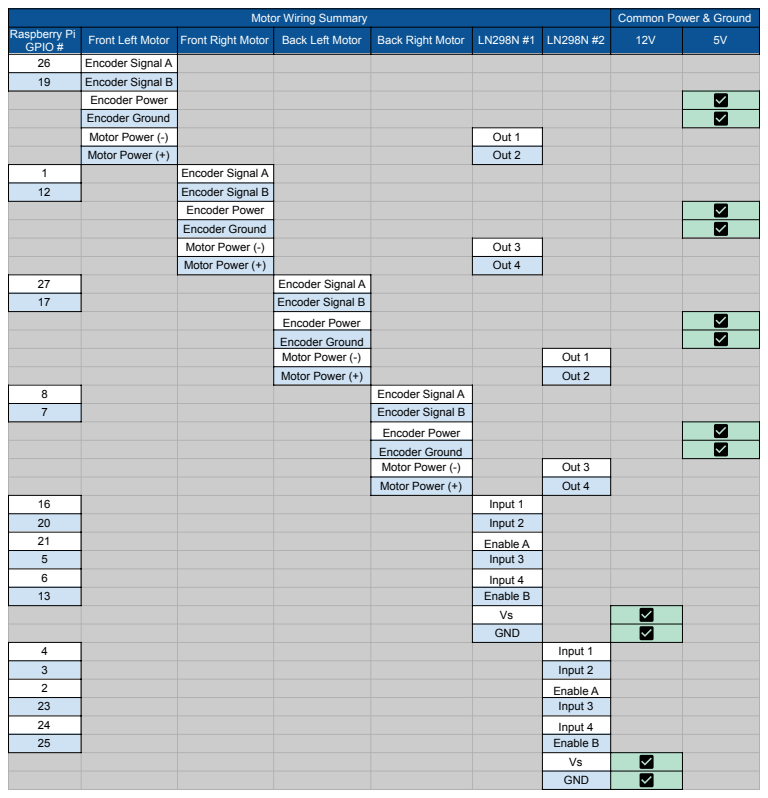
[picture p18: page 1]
Encoder Power; Encoder Ground; Motor Power (-); Out 1; Motor Power (+); Out 2; Out 3; Out 4; Encoder Signal A; Encoder Signal B; Input 1; Input 2; Enable A; Input 3; Input 4; Enable B; GND

Motor Wiring Summary | Common Power & Ground

Raspberry Pi GPIO # | Front Left Motor | Front Right Motor | Back Left Motor | Back Right Motor | LN298N #1 | LN298N #2 | 12V | 5V

26 | Encoder Signal A
19 | Encoder Signal B

1 | Encoder Signal A
12 | Encoder Signal B

27 | Encoder Signal A
17 | Encoder Signal B

Vs
GND

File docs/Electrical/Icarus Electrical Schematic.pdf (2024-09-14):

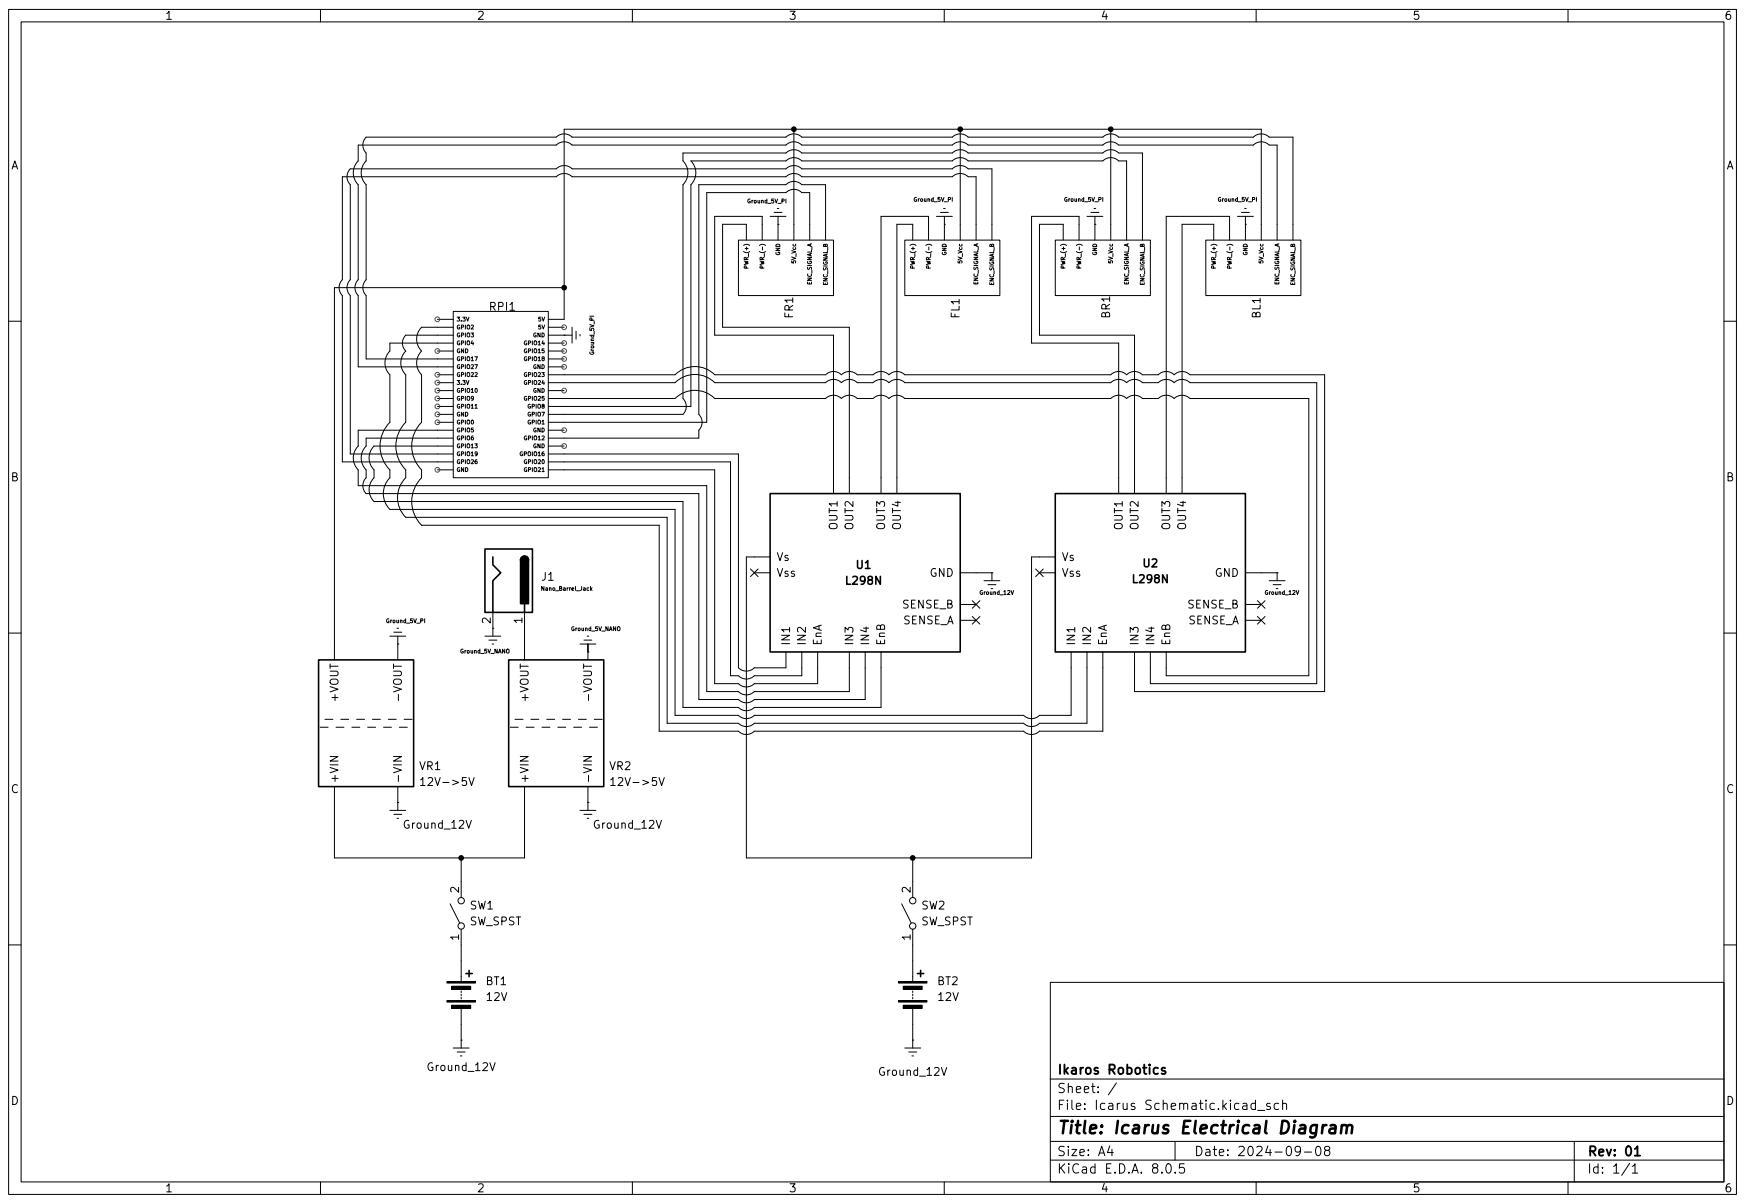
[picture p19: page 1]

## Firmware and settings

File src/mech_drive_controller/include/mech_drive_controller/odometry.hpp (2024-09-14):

// Copyright 2020 PAL Robotics S.L.
//
// Licensed under the Apache License, Version 2.0 (the "License");
// you may not use this file except in compliance with the License.
// You may obtain a copy of the License at
//
//     http://www.apache.org/licenses/LICENSE-2.0
//
// Unless required by applicable law or agreed to in writing, software
// distributed under the License is distributed on an "AS IS" BASIS,
// WITHOUT WARRANTIES OR CONDITIONS OF ANY KIND, either express or implied.
// See the License for the specific language governing permissions and
// limitations under the License.

/*
 * Author: Luca Marchionni
 * Author: Bence Magyar
 * Author: Enrique Fernández
 * Author: Paul Mathieu
 */

#ifndef MECH_DRIVE_CONTROLLER__ODOMETRY_HPP_
#define MECH_DRIVE_CONTROLLER__ODOMETRY_HPP_

#include <cmath>

#include "mech_drive_controller/rolling_mean_accumulator.hpp"
#include "rclcpp/time.hpp"


namespace mech_drive_controller
{
class Odometry
{
public:
  explicit Odometry(size_t velocity_rolling_window_size = 10);

  void init(const rclcpp::Time & time);
  bool update(double front_left_pos, double front_right_pos, double back_left_pos, double back_right_pos, const rclcpp::Time & time);
  void updateOpenLoop(double linear_x, double linear_y, double angular, const rclcpp::Time & time);
  void resetOdometry();

  double getX() const { return x_; }
  double getY() const { return y_; }
  double getHeading() const { return heading_; }
  double getLinear_x() const { return linear_x_; }
  double getLinear_y() const { return linear_y_; }
  double getAngular() const { return angular_; }

  void setWheelParams(double wheel_separation_length, double wheel_seperation_width, double left_wheel_radius, double right_wheel_radius);
  void setVelocityRollingWindowSize(size_t velocity_rolling_window_size);

private:
  using RollingMeanAccumulator = mech_drive_controller::RollingMeanAccumulator<double>;

  void integrateRungeKutta2(double linear_x, double linear_y, double angular);
  void integrateExact(double linear_x, double linear_y, double angular);
  void resetAccumulators();

  // Current timestamp:
  rclcpp::Time timestamp_;

  // Current pose:
  double x_;        //   [m]
  double y_;        //   [m]
  double heading_;  // [rad]

  // Current velocity:
  double linear_x_;   //   [m/s]
  double linear_y_;
  double angular_;  // [rad/s]

  // Wheel kinematic parameters [m]:
  double wheel_separation_length_;
  double wheel_separation_width_;
  double left_wheel_radius_;
  double right_wheel_radius_;

  // Previous wheel position/state [rad]:
  double front_left_wheel_old_pos_;
  double front_right_wheel_old_pos_;
  double back_left_wheel_old_pos_;
  double back_right_wheel_old_pos_;

  // Rolling mean accumulators for the linear and angular velocities:
  size_t velocity_rolling_window_size_;
  RollingMeanAccumulator linear_accumulator_x;
  RollingMeanAccumulator linear_accumulator_y;
  RollingMeanAccumulator angular_accumulator_;
};

}  // namespace mech_drive_controller

#endif  // MECH_DRIVE_CONTROLLER__ODOMETRY_HPP_

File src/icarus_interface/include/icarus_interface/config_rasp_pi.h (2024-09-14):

#ifndef ICARUSINTERFACE_CONFIG_RASP_PI_H
#define ICARUSINTERFACE_CONFIG_RASP_PI_H    
#include "wheel.h"
#include "control_toolbox/pid.hpp"

using control_toolbox::Pid;
//===============================================================
//  STRUCTS
//===============================================================
struct encoder{
    const uint8_t OPTGPIOA; //
    const uint8_t OPTGPIOB; //
    const uint8_t OPTGLITCH; //Constant
};

struct motor{
    const uint16_t PWM_MAX;
    const uint8_t ENA; //enableMotor Pin
    const uint8_t IN1; //forwardPin
    const uint8_t IN2; //backwardPin
    const uint8_t FREQ; //
    const uint16_t RANGE; //
};

//===============================================================
//  CONSTANTS
//===============================================================
//encoder PID value
const double PROPORTIONAL_GAIN = 0;
const double INTERGRAL_GAIN = 0;
const double DERIVATIVE_GAIN = 0;
const double I_MIN = 0.3;
const double I_MAX = -0.3;
const bool ANTIWINDUP = true;

// motor = {PWM_MAX, ENA, IN1, IN2, FREQ, RANGE}
const uint16_t PWM_MAX = 255;
const uint8_t FREQ = 200;
const uint16_t RANGE = 255;

const motor MOTOR_FL = {PWM_MAX, 21, 16, 20, FREQ, RANGE};
const motor MOTOR_FR = {PWM_MAX, 13, 5, 6, FREQ, RANGE};
const motor MOTOR_BL = {PWM_MAX, 2, 4, 3, FREQ, RANGE};
const motor MOTOR_BR = {PWM_MAX, 25, 23, 24, FREQ, RANGE};

// encoder = {OptA, OptB, Glitch}
const uint8_t OPTGLITCH_DEFAULT = 250;

const encoder ENCODER_FL = {26, 19, OPTGLITCH_DEFAULT};
const encoder ENCODER_FR = {1, 12, OPTGLITCH_DEFAULT};
const encoder ENCODER_BL = {27, 17, OPTGLITCH_DEFAULT};
const encoder ENCODER_BR = {8, 7, OPTGLITCH_DEFAULT};


//===============================================================
//  GLOBAL VARIABLES
//===============================================================
extern int pi_;

extern Wheel fl_wheel_;
extern Wheel fr_wheel_;
extern Wheel bl_wheel_;
extern Wheel br_wheel_;
extern int effortFL;

extern control_toolbox::Pid pidFL;
extern control_toolbox::Pid pidBL;
extern control_toolbox::Pid pidFR;
extern control_toolbox::Pid pidBR;

#endif // ICARUSINTERFACE_CONFIG_RASP_PI_H

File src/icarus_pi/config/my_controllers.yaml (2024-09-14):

controller_manager:
  ros__parameters:
    update_rate: 15
    #use_sim_time: true

    mech_cont:
      type: mech_drive_controller/MechDriveController
    
    joint_broad:
      type: joint_state_broadcaster/JointStateBroadcaster

mech_cont:
  ros__parameters:
    publish_rate: 45.0
    base_frame_id: base_link
    odom_frame_id: odom

    wheels_per_side: 2
    front_left_wheel_name: ["frontLeft_joint"]
    front_right_wheel_name: ["frontRight_joint"]
    back_left_wheel_name: ["backLeft_joint"]
    back_right_wheel_name: ["backRight_joint"]
    wheel_separation_width: 0.21
    wheel_separation_length: 0.1665
    wheel_radius: .024
    

    use_stamped_vel: false


    joint_state:
      front_left_wheel:
        topic: "/frontLeft_joint" # Adjust topic names as per your actual topics
        ignore_timestamp: true
      front_right_wheel:
        topic: "/frontRight_joint" # Adjust topic names as per your actual topics
        ignore_timestamp: true
      back_left_wheel:
        topic: "/backLeft_joint" # Adjust topic names as per your actual topics
        ignore_timestamp: true
      back_right_wheel:
        topic: "/backRight_joint" # Adjust topic names as per your actual topics
        ignore_timestamp: true


joint_broad:
  ros__parameters:
    update_rate: 30
    joints: ["frontLeft_joint", "backLeft_joint", "frontRight_joint", "backRight_joint"]

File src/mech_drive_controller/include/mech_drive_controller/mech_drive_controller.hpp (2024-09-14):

// Copyright 2020 PAL Robotics S.L.
//
// Licensed under the Apache License, Version 2.0 (the "License");
// you may not use this file except in compliance with the License.
// You may obtain a copy of the License at
//
//     http://www.apache.org/licenses/LICENSE-2.0
//
// Unless required by applicable law or agreed to in writing, software
// distributed under the License is distributed on an "AS IS" BASIS,
// WITHOUT WARRANTIES OR CONDITIONS OF ANY KIND, either express or implied.
// See the License for the specific language governing permissions and
// limitations under the License.

/*
 * Author: Bence Magyar, Enrique Fernández, Manuel Meraz
 */

#ifndef MECH_DRIVE_CONTROLLER__MECH_DRIVE_CONTROLLER_HPP_
#define MECH_DRIVE_CONTROLLER__MECH_DRIVE_CONTROLLER_HPP_

#include <chrono>
#include <cmath>
#include <memory>
#include <queue>
#include <string>
#include <vector>

#include "controller_interface/controller_interface.hpp"
#include "mech_drive_controller/odometry.hpp"
#include "mech_drive_controller/speed_limiter.hpp"
#include "mech_drive_controller/visibility_control.h"
#include "geometry_msgs/msg/twist.hpp"
#include "geometry_msgs/msg/twist_stamped.hpp"
#include "hardware_interface/handle.hpp"
#include "nav_msgs/msg/odometry.hpp"
#include "odometry.hpp"
#include "rclcpp/rclcpp.hpp"
#include "rclcpp_lifecycle/state.hpp"
#include "realtime_tools/realtime_box.h"
#include "realtime_tools/realtime_buffer.h"
#include "realtime_tools/realtime_publisher.h"
#include "tf2_msgs/msg/tf_message.hpp"

namespace mech_drive_controller
{
using CallbackReturn = rclcpp_lifecycle::node_interfaces::LifecycleNodeInterface::CallbackReturn;

class MechDriveController : public controller_interface::ControllerInterface
{
  using Twist = geometry_msgs::msg::TwistStamped;

public:
  MECH_DRIVE_CONTROLLER_PUBLIC
  MechDriveController();

  MECH_DRIVE_CONTROLLER_PUBLIC
  controller_interface::return_type init(const std::string & controller_name) override;

  MECH_DRIVE_CONTROLLER_PUBLIC
  controller_interface::InterfaceConfiguration command_interface_configuration() const override;

  MECH_DRIVE_CONTROLLER_PUBLIC
  controller_interface::InterfaceConfiguration state_interface_configuration() const override;

  MECH_DRIVE_CONTROLLER_PUBLIC
  controller_interface::return_type update() override;

  MECH_DRIVE_CONTROLLER_PUBLIC
  CallbackReturn on_configure(const rclcpp_lifecycle::State & previous_state) override;

  MECH_DRIVE_CONTROLLER_PUBLIC
  CallbackReturn on_activate(const rclcpp_lifecycle::State & previous_state) override;

  MECH_DRIVE_CONTROLLER_PUBLIC
  CallbackReturn on_deactivate(const rclcpp_lifecycle::State & previous_state) override;

  MECH_DRIVE_CONTROLLER_PUBLIC
  CallbackReturn on_cleanup(const rclcpp_lifecycle::State & previous_state) override;

  MECH_DRIVE_CONTROLLER_PUBLIC
  CallbackReturn on_error(const rclcpp_lifecycle::State & previous_state) override;

  MECH_DRIVE_CONTROLLER_PUBLIC
  CallbackReturn on_shutdown(const rclcpp_lifecycle::State & previous_state) override;

protected:
  struct WheelHandle
  {
    std::reference_wrapper<const hardware_interface::LoanedStateInterface> position;
    std::reference_wrapper<hardware_interface::LoanedCommandInterface> velocity;
  };

  CallbackReturn configure_side(const std::string & side, const std::vector<std::string> & wheel_name, std::vector<WheelHandle> & registered_handles);

  std::vector<std::string> back_left_wheel_name;
  std::vector<std::string> back_right_wheel_name;
  std::vector<std::string> front_left_wheel_name;
  std::vector<std::string> front_right_wheel_name;

  std::vector<WheelHandle> registered_front_left_wheel_handle_;
  std::vector<WheelHandle> registered_front_right_wheel_handle_;
  std::vector<WheelHandle> registered_back_left_wheel_handle_;
  std::vector<WheelHandle> registered_back_right_wheel_handle_;

  struct WheelParams
  {
    size_t wheels_per_side = 0;
    double separation_length = 0.0; //w.r.t. the midpoint of the wheel length
    double separation_width = 0.0; // w.r.t. the midpoint of the wheel width
    double radius = 0.0; //[m]
  } wheel_params_;

  struct OdometryParams
  {
    bool open_loop = false;
    bool enable_odom_tf = true;
    std::string base_frame_id = "base_link";
    std::string odom_frame_id = "odom";
    std::array<double, 6> pose_covariance_diagonal;
    std::array<double, 6> twist_covariance_diagonal;
  } odom_params_;

  Odometry odometry_;

  std::shared_ptr<rclcpp::Publisher<nav_msgs::msg::Odometry>> odometry_publisher_ = nullptr;
  std::shared_ptr<realtime_tools::RealtimePublisher<nav_msgs::msg::Odometry>>
    realtime_odometry_publisher_ = nullptr;

  std::shared_ptr<rclcpp::Publisher<tf2_msgs::msg::TFMessage>> odometry_transform_publisher_ =
    nullptr;
  std::shared_ptr<realtime_tools::RealtimePublisher<tf2_msgs::msg::TFMessage>>
    realtime_odometry_transform_publisher_ = nullptr;

  // Timeout to consider cmd_vel commands old
  std::chrono::milliseconds cmd_vel_timeout_{500};

  bool subscriber_is_active_ = false;
  rclcpp::Subscription<Twist>::SharedPtr velocity_command_subscriber_ = nullptr;
  rclcpp::Subscription<geometry_msgs::msg::Twist>::SharedPtr
    velocity_command_unstamped_subscriber_ = nullptr;

  realtime_tools::RealtimeBox<std::shared_ptr<Twist>> received_velocity_msg_ptr_{nullptr};

  std::queue<Twist> previous_commands_;  // last two commands

  // speed limiters
  SpeedLimiter limiter_linear_;
  SpeedLimiter limiter_angular_;

  bool publish_limited_velocity_ = false;
  std::shared_ptr<rclcpp::Publisher<Twist>> limited_velocity_publisher_ = nullptr;
  std::shared_ptr<realtime_tools::RealtimePublisher<Twist>> realtime_limited_velocity_publisher_ =
    nullptr;

  rclcpp::Time previous_update_timestamp_{0};

  // publish rate limiter
  double publish_rate_ = 50.0;
  rclcpp::Duration publish_period_{0, 0};
  rclcpp::Time previous_publish_timestamp_{0};

  bool is_halted = false;
  bool use_stamped_vel_ = true;

  bool reset();
  void halt();
};
}  // namespace diff_drive_controller
#endif  // MECH_DRIVE_CONTROLLER__MECH_DRIVE_CONTROLLER_HPP_

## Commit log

2023-10-21 included tutorial package
    [gazebo_control.xacro, inertial_macros.xacro, my_controllers.yaml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]
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2024-01-23 Updated Hw Int for 4 motors
    [gazebo_control.xacro, lidar.xacro, my_controllers.yaml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]
2024-01-24 added 4 motor pins to hwi
    [robot_hw_consts.xacro]
2024-02-11 Updated spd calc
    [ros2_control.xacro]
2024-03-01 test motor speed
    [robot_hw_consts.xacro]
2024-03-30 renamed files from my_bot
    [gazebo_control.xacro, inertial_macros.xacro, lidar.xacro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]
2024-04-01 Adding lidar.xacro to the robot.urdf.xacro. Changing spawner to spawner.py in launch_sim.launch.py to be able to run in foxy instead of humble
    [lidar.xacro, robot.urdf.xacro]
2024-05-03 deleted misc build files
    [gazebo_control.xacro, inertial_macros.xacro, lidar.xacro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]
2024-06-01 Added Mecanum Controller
    [my_controllers.yaml, my_controllers_old.yaml, test_diff_drive_controller.yaml]
2024-06-04 Hardware Interface Restructure
    [robot_controller_example.yaml, ros2_control.xacro]
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2024-06-17 added mechanum wheels as urdfs with launch files to test
    [Mecanum - Right.URDF.csv, Mecanum - Right.URDF.urdf, Mecanum_Roller_Link1.STL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]
2024-06-18 fixed file pathing for meshes within urdfs
    [Mecanum - Right.URDF.urdf, Mechanum - Left.URDF.urdf]
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2024-06-18 Added new mecanum urdfs with proper joint positioning
    [Mecanum-Right.csv, Mecanum-Right.urdf, Mecanum_Roller_Link1.STL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]
2024-06-18 fixed urdf description issue that would cause rollers to revolve around the wrong axis
    [Mecanum - Right.URDF.csv, Mecanum - Right.URDF.urdf, Mecanum-Left.csv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]
2024-06-19 Configured urdf files to work in ros2 with controller manager edited sim launch for testing wheel urdfs created rsp.wheel.py launch file for wheels for testing
    [Mecanum-Left.urdf.xacro, Mecanum-Right.csv, Mecanum-Right.urdf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]
2024-06-30 added Y and Yaw calulcations to odometry package
2024-07-01 added variables linear_y and linear_x to fix build issues
    [odometry.hpp]
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2024-07-01 changed ros update rate because messages kept dropping
    [controllers.yaml, my_controllers.yaml]
2024-07-01 alterred velocity calculations to divide by time within estimation functions
    corrected Y velocity and X velocity math
2024-07-02 Fixed Odom twist messages
    [lidar.xacro, my_controllers.yaml, robot_core.xacro]
2024-07-09 added proper wheel geometry vals
    [my_controllers.yaml, robot_controller_example.yaml]
2024-07-12 Fixed Lidar Not Rendering
    [lidar.xacro, my_controllers.yaml]
2024-07-12 lidar location fix
    [lidar.xacro]
2024-07-13 Added gazebo planar plugin to ros2_control.xacro. Modified wheel joints to be fixed in sim and continuous in real world in robot_core.xacro. Cleaned up and added link materials in gazebo_control.xacr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
    [gazebo_control.xacro, lidar.xacro, robot_core.xacro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]
2024-07-13 corrected incorrect odom reading issue
    [lidar.xacro, my_controllers.yaml, robot_core.xacro]
2024-07-15 fixed angular drift accumulated error
    [lidar.xacro, my_controllers.yaml, robot_core.xacro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]
2024-07-18 Split the planar and ros2 control into two seperate descriptions for easy launch
    [gazebo_control.xacro, gazebo_robot_core.xacro, robot.urdf.xacro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]
2024-07-20 odom parameter tuning
    [lidar.xacro, my_controllers.yaml, robot_core.xacro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]
2024-07-28 Created branch for PID implementation
    added effort variable within wheel class
    created desired_speed variablele within
    wheel class
    changed set motor command to use effort values
2024-07-29 Squashed commit of the following:
    commit 6478a12120643f634f0931956185b81d629095a3
    Author: steel <steel_blu@live.com>
    Date: Thu Jul 18 17:51:12 2024 -0500
    Split the planar and ros2 control into two seperate descriptions for easy launch
    [gazebo_control.xacro, gazebo_robot_core.xacro, robot.urdf.xacro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]
2024-07-30 - added control toolbox to config_rasp_pi.h extern values placed here, control_toolbox objects are updated within encoder_control.cpp
    -added time_difference member to wheel object
    -removed unused variables from encoder_control.cpp
    -time difference now is updating to the time difference variable within the wheel object
    - time difference object variable is now used within computeCommand
    -computeCommand line now directly updates effort variable within wheel object
    -added pid computation within icarus_HW_Interface.cpp to circumvent issue where effort was never updating since it needed wheels to move first
    -debug messages to check effort values
    [Icarus_HW_Interface.cpp, config_rasp_pi.h, encoder_control.cpp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]
2024-08-03 added sensor messages topic to track current velocity and effort of wheels
2024-08-05 fixed effort and measured velocity values, as wella s desired speed values
    [ros2_control.xacro]
2024-08-05 started pid tuning mirrors PID computation onto all wheels a lot of debugging prints added modified how motors recieved pwm
2024-08-06 icarus_HW file doesnt compute eff values correctly
    [Icarus_HW_Interface.cpp, encoder_control.cpp]
2024-08-07 moved calculations performed in encoder control over the hw interface
2024-08-09 created custom PID calcualtions to circumvent control toolbox issues
    [Icarus_HW_Interface.cpp, config_rasp_pi.h, encoder_control.cpp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]
2024-08-09 effort calcualtion moved to only be done within main hardware file pid tuning for P parameter only
2024-08-09 PID applied to all 4 wheels -removed some calculations from encoder ocntrol to reduce CPU load -tuning parameters need to be edited still
2024-08-10 added custom message interface for PID tracking to ahrdware interface code
2024-08-10 corrected pid names to reflect pid measurements
    enabled power to back left motor
    reset pid config params
    fixed error where measured velocity values spike to outrageous numbers. removed velocity measurement from encoderclock files
    [Icarus_HW_Interface.cpp, config_rasp_pi.h, encoder_control.cpp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]
2024-08-10 encoder callbacl functions now only ever return the current encoder
    position calculation moved to icarus hardware interface
2024-08-10 encoder callback functions now only ever return the current encoder
    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
2024-08-12 added power back to all wheels pid tuning changed update rate of controller to smoothen pid measurements
    [my_controllers.yaml]
2024-08-13 retuned cmd to joint vel
    [my_controllers.yaml]
2024-08-13 fixed mecanum sim urdf
    [robot.urdf.xacro]
2024-08-14 Corrected Odometry angular velocity forwardm kinematics equation
2024-08-16 Updated mech contoller update rate
    [my_controllers.yaml]
2024-08-17 - flipped direction of odometry frame so that robot now moves in the positive directions of the odometry frame when given a positive command (same for negative commands) - changed robot dimensions wi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
    [my_controllers.yaml, robot_core.xacro]
2024-08-21 Updating publish rate & dimensions in my_controllers. Changing the nav2 mux topic to cmd_vel in mux.yaml. Changed power thresholds for motor_control.cpp. Fixed the elapsed time calculation in hw_inte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
    [my_controllers.yaml]
2024-08-24 flipped robot direction and wheels
    [lidar.xacro, robot_core.xacro]
2024-08-24 flipped the lidar to match with its pre-defined hardware axis
    [lidar.xacro]
2024-08-24 Removed negative values from linear_x and linear_y in odometry.cpp
2024-08-25 Changed integrateExact in odom to match derivations used for omni wheeled robots
2024-08-27 Updated wheel separation width my_controllers.yaml. Updated y limiter to use linear.y rather than angular.y.
    [my_controllers.yaml]
2024-08-30 Updated Robot Core Wheel Positions
    [gazebo_robot_core.xacro]
2024-09-02 Updated Package xml
    removed controllersfolder from icarus_interface
    removed unused params from controller example yaml
    removed comments and unused variables from encoder controll.cpp
    added PID trackers for all wheels in hardware interface.cpp
    removed debuggers and commented out code from icarus harware interface.cpp
    removed comment from motor control.cpp
    put in correct package into package.xml
    removed multiplier variables from wheelparam struct in mech drive controller.hpp
    removed logger variables from odometry hpp file
    removed wheel multiplier parameter calls from mech drive controller.cpp
    removeed logger values and commented out code from odometry.cpp
    added clarity to integratio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
    [my_controllers_old.yaml, robot_controller_example.yaml]
2024-09-06 added camera to urdf
    [camera.xacro, robot.urdf.xacro]
2024-09-08 commented in expected units for wheel.h comments added for icarus interface, time calculation updated added comments mech drive controller hpp file, visual clarity cleanups added comments mech drive 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
2024-09-10 added electrical schematic comments on mech drive controller added odom cpp comments
2024-09-12 Added pigpio zip file needed for PiGPIO-d. Added electrical schematic, diagram, and table to summary motor corrections
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2024-09-12 Update README.md to add Mecanum wheel section & references
2024-09-13 added mechanical STL files and assembly visual
    [Battery Holder V2.STL, Buck Converter Holder.STL, L298 Holder.stl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]
2024-09-13 Rename L298 Holder.stl to L298N Holder.stl
    [L298N Holder.stl]
2024-09-13 Adding Mechanical Assembly as Image so I can embed it into Readme
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2024-09-13 added camera mount stl
    [Camera Mount.STL]
2024-09-16 Reuploading mecanum wheel kinematic model Muib addded, but in docs
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
